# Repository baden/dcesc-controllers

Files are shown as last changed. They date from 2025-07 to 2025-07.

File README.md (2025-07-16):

# dcesc-controllers

Тут буде і плата і програма.

## Так. Шось в процесі ми якось дішли до потужної плати. І назва трохи не відповідає.

## Мотори

Експериментую з моторами з редуктором.

Починаю експерімент з [JGA25-370](https://www.aliexpress.com/item/1005006961499514.html)
та [GA24Y-370](https://www.aliexpress.com/item/1005005835525169.html)

на двигунах діаметром 24.4мм

Ціль:
напруга живлення - 24В
струм - 3А
керування - RS485

Хотілось би CAN, але поки не підібрани варіанти конролера.

Пропонується варіанти драйвера двигуна:

- [DRV8870DDAR](https://www.kosmodrom.ua/mikroshema-kontrolera-dviguna/drv8870ddar-4.html) - 12грн
- [DRV8874PWPR](https://www.kosmodrom.ua/mikroshema-kontrolera-dviguna/drv8874pwpr-2.html) - 44грн

# Робимо цю версію на готових драйверах. Бо два-три мотори на одному мікроконтроллері то дуже складно.

## На майбутньє, може буду підбирати якісь китайські компоненти, бо ціна на амеріканських брендах виходить якась зовсім неадекватна.

## Встановлення інструментів

https://github.com/riscv-software-src/homebrew-riscv

```bash
brew tap riscv-software-src/riscv
brew install riscv-tools
brew install riscv-openocd
brew test riscv-tools
/opt/homebrew/opt/riscv-gnu-toolchain/bin/riscv64-unknown-elf-gcc --version
```

/opt/homebrew/opt/riscv-openocd/bin/openocd

## Обираємо мікроконтролер

Я ще не визначився, чи треба робити виключно на CAN, чи може обійтись RS485.

- Оцей мабуть ідеальний для контролеру двигуна
https://www.kosmodrom.ua/mikrokontroler/stm32g431cbt6.html

Для плат с готовий драйвером двигуна, контролер:

https://www.kosmodrom.ua/mikrokontroler/stm32f042f6p6.html

- Шось мегапопулярне, але не впевнен шо воно.
https://www.kosmodrom.ua/mikrokontroler/stm32f103c8t6.html

- Ексотіка для ізвращьєнців
https://www.kosmodrom.ua/mikrokontroler/gd32f103cbt6-2.html

Ще подивлюсь на цей: CH32V203. Здається є сумісний по ногам як STM, так і GD, так і AT

## Обираємо транзистор на потужну плату

### 60 V

https://www.kosmodrom.ua/tranzistor-poloviy-mosfet/60n06-2.html, 39 nC, 14mOhm
https://www.kosmodrom.ua/tranzistor-poloviy-mosfet/csd18537nq5a-2.html, 18 nC, 13mOhm
https://www.kosmodrom.ua/tranzistor-poloviy-mosfet/aon7262e-2.html, 45 nC, 6.2mOhm

## Драйвер MOSFET

https://www.kosmodrom.ua/drayveri-igbt-mosfet/eg3013s-2.html, 0.8/1.0A,

## Драйвер CAN-шини.

Треба або взяти 3.3В CAN, ти живити окремим живленням 5V, та обирати з Vio, чи согласовувати рівні.

https://www.kosmodrom.ua/interfeys-can-2/sn65hvd230dr.html
https://www.kosmodrom.ua/interfeys-can-2/sn65hvd232d.html (no stb and sleep)

## Готовий контролер на слабкіший мотор

https://www.kosmodrom.ua/mikroshema-kontrolera-dviguna/drv8870ddar-4.html, 3.6А, 45V
https://www.kosmodrom.ua/mikroshema-kontrolera-dviguna/drv8870ddar-2.html,
https://www.kosmodrom.ua/mikroshema-kontrolera-dviguna/drv8874pwpr-2.html, 6А, 37V

## Всіляке різне

https://www.kosmodrom.ua/tranzistor-poloviy-mosfet/ao4828.html, дешевий сдвоєний мосфет на драйвер до 3А.

https://www.kosmodrom.ua/stabilizator-naprugi/ht7533s-umw-2.html, Стабілізатор напруги на процесор, 3.3V, 0.1A

## Во, подивиться це

https://github.com/wagiminator/CH32V003-GameConsole/tree/main

Ще це:
https://github.com/wagiminator/MCU-Templates

Ще тут купа посилань:
https://github.com/wagiminator/Development-Boards/tree/main/CH32V003A4M6_DevBoard

https://github.com/AlessandroAU/ESP32-CRSF-Packet-Gen/blob/master/CRSF_testcode/CRSF.h
https://px4.github.io/Firmware-Doxygen/d9/dd2/crsf_8cpp_source.html

https://github.com/vedderb/bldc_uart_comm_stm32f4_discovery/blob/c19a6283e187040f25aa52e213673938db054d06/bldc_interface.c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

https://vedder.se/2015/10/communicating-with-the-vesc-using-uart/

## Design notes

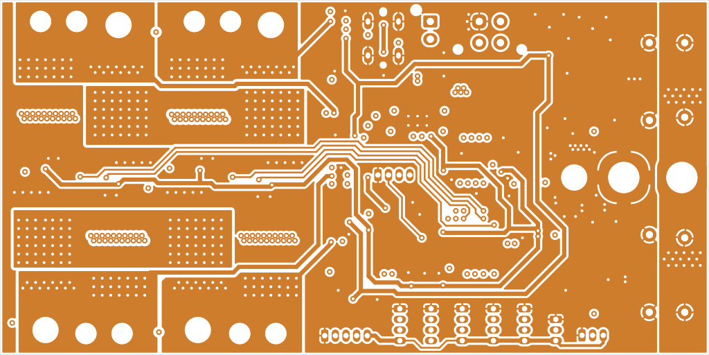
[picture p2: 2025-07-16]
dist/dcesc-ga25/check/dcesc-ga25-In2.Cu.png

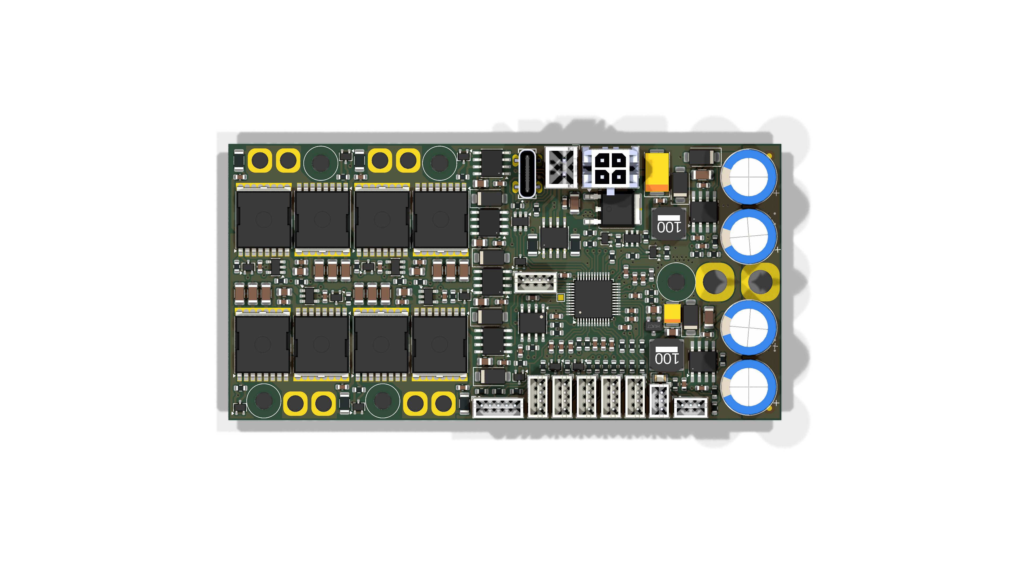
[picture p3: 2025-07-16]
boards/dcesc-ga25/dcesc-ga25-v0/dcesc-ga25-0.png

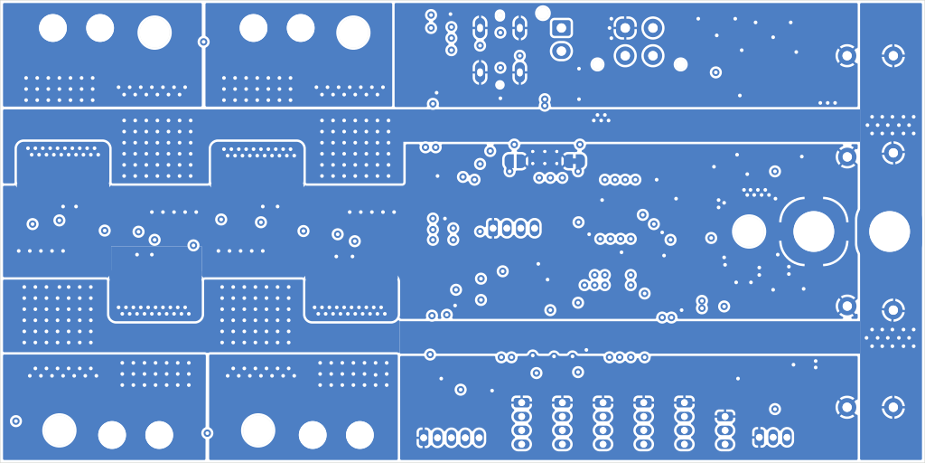
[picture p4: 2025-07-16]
dist/dcesc-ga25/check/dcesc-ga25-B.Cu.png

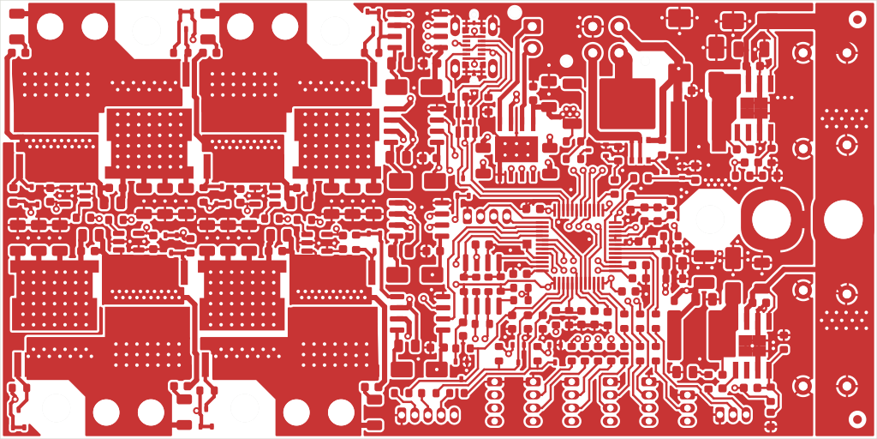
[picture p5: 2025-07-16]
dist/dcesc-ga25/check/dcesc-ga25-F.Cu.png

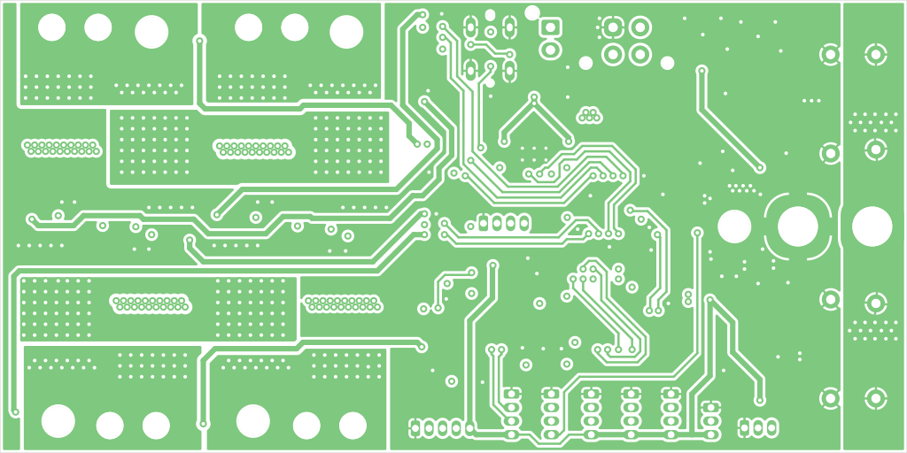
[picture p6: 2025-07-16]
dist/dcesc-ga25/check/dcesc-ga25-In1.Cu.png

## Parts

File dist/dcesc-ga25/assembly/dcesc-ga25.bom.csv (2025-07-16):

Refs | Value | Footprint | Qty | DNP
C1 | 10uF | Capacitor_SMD:C_1206_3216Metric | 1
C2 | 10uF | Capacitor_SMD:C_1206_3216Metric | 1
C3 | 0.1uF | Capacitor_SMD:C_0603_1608Metric | 1
C4 | 0.1uF | Capacitor_SMD:C_0603_1608Metric | 1
C5 | 0.1uF | Capacitor_SMD:C_0603_1608Metric | 1
C6 | 0.1uF | Capacitor_SMD:C_0603_1608Metric | 1
C7 | 82p | Capacitor_SMD:C_0603_1608Metric | 1
C8 | 82p | Capacitor_SMD:C_0603_1608Metric | 1
C9 | 100uF | Capacitor_Tantalum_SMD:CP_EIA-7343-15_Kemet-W | 1
C10 | 0.1uF | Capacitor_SMD:C_0603_1608Metric | 1
C11 | 100uF | Capacitor_Tantalum_SMD:CP_EIA-3528-12_Kemet-T | 1
C12 | 10uF | Capacitor_SMD:C_0805_2012Metric | 1
C13 | 10uF | Capacitor_SMD:C_0805_2012Metric | 1
C14 | 10uF | Capacitor_SMD:C_1206_3216Metric | 1
C15 | 0.1uF | Capacitor_SMD:C_0603_1608Metric | 1
C16 | 0.1uF | Capacitor_SMD:C_0603_1608Metric | 1
C17 | 0.1uF | Capacitor_SMD:C_0603_1608Metric | 1
C18 | 0.1uF | Capacitor_SMD:C_0603_1608Metric | 1
C19 | 0.1uF | Capacitor_SMD:C_0603_1608Metric | 1
C20 | 0.1uF | Capacitor_SMD:C_0603_1608Metric | 1
C21 | 0.1uF | Capacitor_SMD:C_0603_1608Metric | 1
C22 | 10nF | Capacitor_SMD:C_0603_1608Metric | 1
C23 | 10nF | Capacitor_SMD:C_0603_1608Metric | 1
C24 | 10nF | Capacitor_SMD:C_0603_1608Metric | 1
C25 | 0.1uF | Capacitor_SMD:C_0603_1608Metric | 1
C26 | 10nF | Capacitor_SMD:C_0603_1608Metric | 1
C27 | 0.1uF | Capacitor_SMD:C_0603_1608Metric | 1
C28 | 0.1uF | Capacitor_SMD:C_0603_1608Metric | 1
C29 | 0.1uF | Capacitor_SMD:C_0603_1608Metric | 1
C30 | 0.1uF | Capacitor_SMD:C_0603_1608Metric | 1
C31 | 0.1uF | Capacitor_SMD:C_0603_1608Metric | 1
C32 | 0.1uF | Capacitor_SMD:C_0603_1608Metric | 1
C33 | 0.1uF | Capacitor_SMD:C_0603_1608Metric | 1
C34 | 0.1uF | Capacitor_SMD:C_0603_1608Metric | 1
C35 | 0.1uF | Capacitor_SMD:C_0603_1608Metric | 1
C36 | 0.1uF | Capacitor_SMD:C_0603_1608Metric | 1
C37 | 0.1uF | Capacitor_SMD:C_0603_1608Metric | 1
C38 | 0.1uF | Capacitor_SMD:C_0603_1608Metric | 1
C39 | 0.1uF | Capacitor_SMD:C_0603_1608Metric | 1
C40 | 0.1uF | Capacitor_SMD:C_0603_1608Metric | 1
C41 | 33nF | Capacitor_SMD:C_0603_1608Metric | 1
C42 | 33nF | Capacitor_SMD:C_0603_1608Metric | 1
C43 | 33nF | Capacitor_SMD:C_0603_1608Metric | 1
C44 | 33nF | Capacitor_SMD:C_0603_1608Metric | 1
C45 | 10uF | Capacitor_SMD:C_0805_2012Metric | 1
C46 | 10uF | Capacitor_SMD:C_0805_2012Metric | 1
C47 | 10uF | Capacitor_SMD:C_0805_2012Metric | 1
C48 | 10uF | Capacitor_SMD:C_0805_2012Metric | 1
C49 | 1uF | Capacitor_SMD:C_0805_2012Metric | 1
C50 | 1uF | Capacitor_SMD:C_0805_2012Metric | 1
C51 | 1uF | Capacitor_SMD:C_0805_2012Metric | 1
C52 | 1uF | Capacitor_SMD:C_0805_2012Metric | 1
C53 | 10uF | Capacitor_SMD:C_1206_3216Metric | 1
C54 | 10uF | Capacitor_SMD:C_1206_3216Metric | 1
C55 | 10uF | Capacitor_SMD:C_1206_3216Metric | 1
C56 | 10uF | Capacitor_SMD:C_1206_3216Metric | 1
C57 | 10uF | Capacitor_SMD:C_1206_3216Metric | 1
C58 | 10uF | Capacitor_SMD:C_1206_3216Metric | 1
C59 | 10uF | Capacitor_SMD:C_1206_3216Metric | 1
C60 | 10uF | Capacitor_SMD:C_1206_3216Metric | 1
C61 | 10uF | Capacitor_SMD:C_1206_3216Metric | 1
C62 | 10uF | Capacitor_SMD:C_1206_3216Metric | 1
C63 | 10uF | Capacitor_SMD:C_1206_3216Metric | 1
C64 | 10uF | Capacitor_SMD:C_1206_3216Metric | 1
C65 | 220uF | Capacitor_THT:CP_Radial_D10.0mm_P5.00mm | 1
C66 | 220uF | Capacitor_THT:CP_Radial_D10.0mm_P5.00mm | 1
C67 | 220uF | Capacitor_THT:CP_Radial_D10.0mm_P5.00mm | 1
C68 | 220uF | Capacitor_THT:CP_Radial_D10.0mm_P5.00mm | 1
C69 | 3.3nF | Capacitor_SMD:C_0603_1608Metric | 1
C70 | 3.3nF | Capacitor_SMD:C_0603_1608Metric | 1
C71 | 3.3nF | Capacitor_SMD:C_0603_1608Metric | 1
C72 | 3.3nF | Capacitor_SMD:C_0603_1608Metric | 1
D1 | SMAJ28A | Diode_SMD:D_SMA | 1
D2 | SS24 | Diode_SMD:D_SMA | 1
D3 | SS24 | Diode_SMD:D_SMA | 1
D4 | BAT54SW | Package_TO_SOT_SMD:SOT-323_SC-70 | 1
D5 | BAT54SW | Package_TO_SOT_SMD:SOT-323_SC-70 | 1
D6 | BAT54SW | Package_TO_SOT_SMD:SOT-323_SC-70 | 1
D7 | BAT54AW | Package_TO_SOT_SMD:SOT-323_SC-70 | 1
D8 | BAT54AW | Package_TO_SOT_SMD:SOT-323_SC-70 | 1
D9 | BAT54AW | Package_TO_SOT_SMD:SOT-323_SC-70 | 1
D10 | BAT54AW | Package_TO_SOT_SMD:SOT-323_SC-70 | 1
D11 | BAT54AW | Package_TO_SOT_SMD:SOT-323_SC-70 | 1
D12 | BAT54AW | Package_TO_SOT_SMD:SOT-323_SC-70 | 1
D13 | BAT54AW | Package_TO_SOT_SMD:SOT-323_SC-70 | 1
D14 | BAT54AW | Package_TO_SOT_SMD:SOT-323_SC-70 | 1
D15 | SS24 | Diode_SMD:D_SMA | 1
D16 | SS24 | Diode_SMD:D_SMA | 1
D17 | SS24 | Diode_SMD:D_SMA | 1
D18 | SS24 | Diode_SMD:D_SMA | 1
D19 | BAT54AW | Package_TO_SOT_SMD:SOT-323_SC-70 | 1
D20 | LED | LED_SMD:LED_0805_2012Metric | 1
FB1 | FerriteBead | Inductor_SMD:L_0603_1608Metric | 1
J1 | Jumper_2_Open | Jumper:SolderJumper-2_P1.3mm_Open_RoundedPad1.0x1.5mm | 1
J2 | Jumper_2_Bridged | Jumper:SolderJumper-2_P1.3mm_Bridged_RoundedPad1.0x1.5mm | 1
J3 | Conn_01x01_Socket | Connector_Wire:SolderWire-2.5sqmm_1x01_D2.4mm_OD4.4mm | 1
J4 | Conn_01x01_Socket | Connector_Wire:SolderWire-2.5sqmm_1x01_D2.4mm_OD4.4mm | 1
J5 | Conn_01x01_Socket | Connector_Wire:SolderWire-2.5sqmm_1x01_D2.4mm_OD4.4mm | 1
J6 | Conn_01x01_Socket | Connector_Wire:SolderWire-2.5sqmm_1x01_D2.4mm_OD4.4mm | 1
J7 | Conn_01x01_Socket | Connector_Wire:SolderWire-2.5sqmm_1x01_D2.4mm_OD4.4mm | 1
J8 | Conn_01x01_Socket | Connector_Wire:SolderWire-2.5sqmm_1x01_D2.4mm_OD4.4mm | 1
J9 | Conn_01x01_Socket | Connector_Wire:SolderWire-2.5sqmm_1x01_D2.4mm_OD4.4mm | 1
J10 | Conn_01x01_Socket | Connector_Wire:SolderWire-2.5sqmm_1x01_D2.4mm_OD4.4mm | 1
J18 | Conn_01x01_Socket | Connector_Wire:SolderWire-6sqmm_1x01_D3.5mm_OD7mm | 1
J19 | Conn_01x01_Socket | Connector_Wire:SolderWire-6sqmm_1x01_D3.5mm_OD7mm | 1
L1 | 10uH | locals:Inductor_NR6028T100M | 1
L2 | 10uH | locals:Inductor_NR6028T100M | 1
R1 | 30k | Resistor_SMD:R_0603_1608Metric | 1
R2 | 3.3k | Resistor_SMD:R_0603_1608Metric | 1
R3 | 100k | Resistor_SMD:R_0603_1608Metric | 1
R4 | 10k | Resistor_SMD:R_0603_1608Metric | 1
R5 | 3.3k | Resistor_SMD:R_0603_1608Metric | 1
R6 | 100k | Resistor_SMD:R_0603_1608Metric | 1
R7 | 30k | Resistor_SMD:R_0603_1608Metric | 1
R8 | 30k | Resistor_SMD:R_0603_1608Metric | 1
R9 | 100k | Resistor_SMD:R_0603_1608Metric | 1
R10 | 100k | Resistor_SMD:R_0603_1608Metric | 1
R11 | 100k | Resistor_SMD:R_0603_1608Metric | 1
R12 | 30k | Resistor_SMD:R_0603_1608Metric | 1
R13 | 30k | Resistor_SMD:R_0603_1608Metric | 1
R14 | 0.51R | Resistor_SMD:R_1206_3216Metric | 1
R15 | 1R | Resistor_SMD:R_1206_3216Metric | 1
R16 | 120 | Resistor_SMD:R_0603_1608Metric | 1
R17 | 330k | Resistor_SMD:R_0603_1608Metric | 1
R18 | 10k | Resistor_SMD:R_0603_1608Metric | 1
R19 | 10k | Resistor_SMD:R_0603_1608Metric | 1
R20 | 10k | Resistor_SMD:R_0603_1608Metric | 1
R21 | 30k | Resistor_SMD:R_0603_1608Metric | 1
R22 | 100k | Resistor_SMD:R_0603_1608Metric | 1
R23 | 100k | Resistor_SMD:R_0603_1608Metric | 1
R24 | 100k | Resistor_SMD:R_0603_1608Metric | 1
R25 | 100 | Resistor_SMD:R_0603_1608Metric | 1
R26 | 100 | Resistor_SMD:R_0603_1608Metric | 1
R27 | 100 | Resistor_SMD:R_0603_1608Metric | 1
R28 | 100 | Resistor_SMD:R_0603_1608Metric | 1
R29 | 100 | Resistor_SMD:R_0603_1608Metric | 1
R30 | 100 | Resistor_SMD:R_0603_1608Metric | 1
R31 | 100 | Resistor_SMD:R_0603_1608Metric | 1
R32 | 100 | Resistor_SMD:R_0603_1608Metric | 1
R33 | 100 | Resistor_SMD:R_0603_1608Metric | 1
R34 | 100 | Resistor_SMD:R_0603_1608Metric | 1
R35 | 330k | Resistor_SMD:R_0603_1608Metric | 1
R36 | 30k | Resistor_SMD:R_0603_1608Metric | 1
R37 | 1k | Resistor_SMD:R_0603_1608Metric | 1
R38 | 1k | Resistor_SMD:R_0603_1608Metric | 1
R39 | 1k | Resistor_SMD:R_0603_1608Metric | 1
R40 | 1k | Resistor_SMD:R_0603_1608Metric | 1
R41 | 1k | Resistor_SMD:R_0603_1608Metric | 1
R42 | 100k | Resistor_SMD:R_0603_1608Metric | 1
R43 | 10 | Resistor_SMD:R_0603_1608Metric | 1
R44 | 10 | Resistor_SMD:R_0603_1608Metric | 1
R45 | 10 | Resistor_SMD:R_0603_1608Metric | 1
R46 | 10 | Resistor_SMD:R_0603_1608Metric | 1
R47 | 10 | Resistor_SMD:R_0603_1608Metric | 1
R48 | 10 | Resistor_SMD:R_0603_1608Metric | 1
R49 | 10 | Resistor_SMD:R_0603_1608Metric | 1
R50 | 10 | Resistor_SMD:R_0603_1608Metric | 1
R51 | 3 | Resistor_SMD:R_1206_3216Metric | 1
R52 | 3 | Resistor_SMD:R_1206_3216Metric | 1
R53 | 3 | Resistor_SMD:R_1206_3216Metric | 1
R54 | 3 | Resistor_SMD:R_1206_3216Metric | 1
R55 | 5.1k | Resistor_SMD:R_0603_1608Metric | 1
R56 | 5.1k | Resistor_SMD:R_0603_1608Metric | 1
R57 | 3.3k | Resistor_SMD:R_0603_1608Metric | 1
T1 | IPT012N08N5 | Package_TO_SOT_SMD:Infineon_PG-HSOF-8-1 | 1
T2 | IPT012N08N5 | Package_TO_SOT_SMD:Infineon_PG-HSOF-8-1 | 1
T3 | IPT012N08N5 | Package_TO_SOT_SMD:Infineon_PG-HSOF-8-1 | 1
T4 | IPT012N08N5 | Package_TO_SOT_SMD:Infineon_PG-HSOF-8-1 | 1
T5 | IPT012N08N5 | Package_TO_SOT_SMD:Infineon_PG-HSOF-8-1 | 1
T6 | IPT012N08N5 | Package_TO_SOT_SMD:Infineon_PG-HSOF-8-1 | 1
T7 | IPT012N08N5 | Package_TO_SOT_SMD:Infineon_PG-HSOF-8-1 | 1
T8 | IPT012N08N5 | Package_TO_SOT_SMD:Infineon_PG-HSOF-8-1 | 1
T9 | BC847AW | Package_TO_SOT_SMD:SOT-323_SC-70 | 1
T10 | BC847AW | Package_TO_SOT_SMD:SOT-323_SC-70 | 1
T11 | IRF5803TRPBF | Package_SO:TSOP-6_1.65x3.05mm_P0.95mm | 1
T12 | AOD4185 | Package_TO_SOT_SMD:TO-252-2 | 1
TP1 | BOOT0 | TestPoint:TestPoint_Pad_1.0x1.0mm | 1
U1 | ST1S14PHR | Package_SO:TI_SO-PowerPAD-8 | 1
U2 | ST1S14PHR | Package_SO:TI_SO-PowerPAD-8 | 1
U3 | MCP1703A-3302 | locals:MCP1703 | 1
U4 | STM32G431C8Tx | Package_QFP:LQFP-48_7x7mm_P0.5mm | 1
U5 | INA180A4 | Package_TO_SOT_SMD:SOT-23-5 | 1
U6 | INA180A4 | Package_TO_SOT_SMD:SOT-23-5 | 1
U7 | INA180A4 | Package_TO_SOT_SMD:SOT-23-5 | 1
U8 | INA180A4 | Package_TO_SOT_SMD:SOT-23-5 | 1
U9 | EG3112 | Package_SO:SOP-8_3.9x4.9mm_P1.27mm | 1
U10 | EG3112 | Package_SO:SOP-8_3.9x4.9mm_P1.27mm | 1
U11 | EG3112 | Package_SO:SOP-8_3.9x4.9mm_P1.27mm | 1
U12 | EG3112 | Package_SO:SOP-8_3.9x4.9mm_P1.27mm | 1
U13 | DRV8870DDA | Package_SO:Texas_HTSOP-8-1EP_3.9x4.9mm_P1.27mm_EP2.95x4.9mm_Mask2.4x3.1mm_ThermalVias | 1
U14 | ATA6561-GAQW-N | Package_SO:SOIC-8_3.9x4.9mm_P1.27mm | 1
U15 | USBLC6-2SC6 | Package_TO_SOT_SMD:SOT-23-6 | 1
X1 | Conn_02x02_Top_Bottom | Connector_Molex:Molex_Micro-Fit_3.0_43045-0412_2x02_P3.00mm_Vertical | 1
X2 | Conn_01x03 | Connector_JST:JST_XH_B2B-XH-AM_1x02_P2.50mm_Vertical | 1
X3 | Conn_01x03 | Connector_JST:JST_ZH_B4B-ZR_1x04_P1.50mm_Vertical | 1
X4 | Conn_01x03 | Connector_JST:JST_ZH_B4B-ZR_1x04_P1.50mm_Vertical | 1
X5 | Conn_01x03 | Connector_JST:JST_ZH_B4B-ZR_1x04_P1.50mm_Vertical | 1
X6 | Conn_01x03 | Connector_JST:JST_ZH_B4B-ZR_1x04_P1.50mm_Vertical | 1
X7 | Conn_01x03 | Connector_JST:JST_ZH_B4B-ZR_1x04_P1.50mm_Vertical | 1
X8 | Conn_01x03 | Connector_JST:JST_ZH_B3B-ZR_1x03_P1.50mm_Vertical | 1
X9 | Conn_01x03 | Connector_JST:JST_ZH_B3B-ZR_1x03_P1.50mm_Vertical | 1
X10 | Conn_01x03 | Connector_JST:JST_ZH_B5B-ZR_1x05_P1.50mm_Vertical | 1
X11 | Conn_01x03 | Connector_JST:JST_ZH_B4B-ZR_1x04_P1.50mm_Vertical | 1
X12 | USB4120-03-C_REVA | locals:GCT_USB4120-03-C_REVA | 1

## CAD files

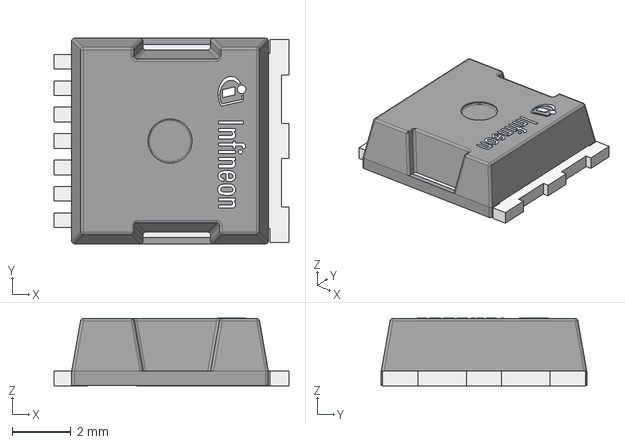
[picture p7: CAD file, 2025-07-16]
boards/dcesc-ga25/3dshapes/PG-HSOF-7-1_Z8B00189574_V04_3D.stp
8.00 x 7.00 x 2.31 mm

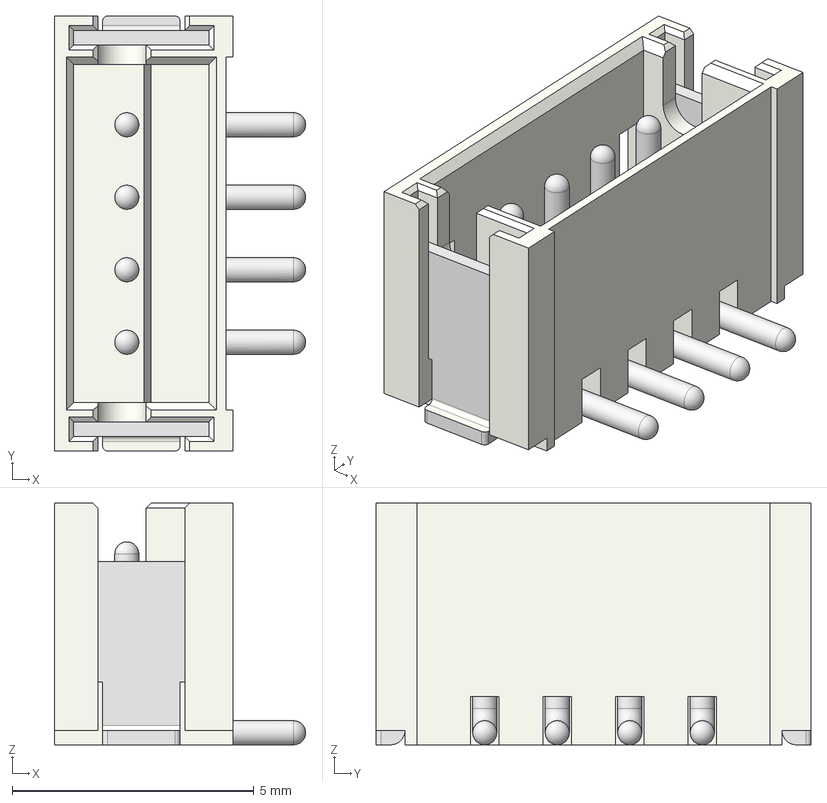
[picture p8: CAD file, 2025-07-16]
boards/dcesc-ga25/3dshapes/B4B-ZR-SM4-TF.step
5.20 x 9.00 x 5.00 mm

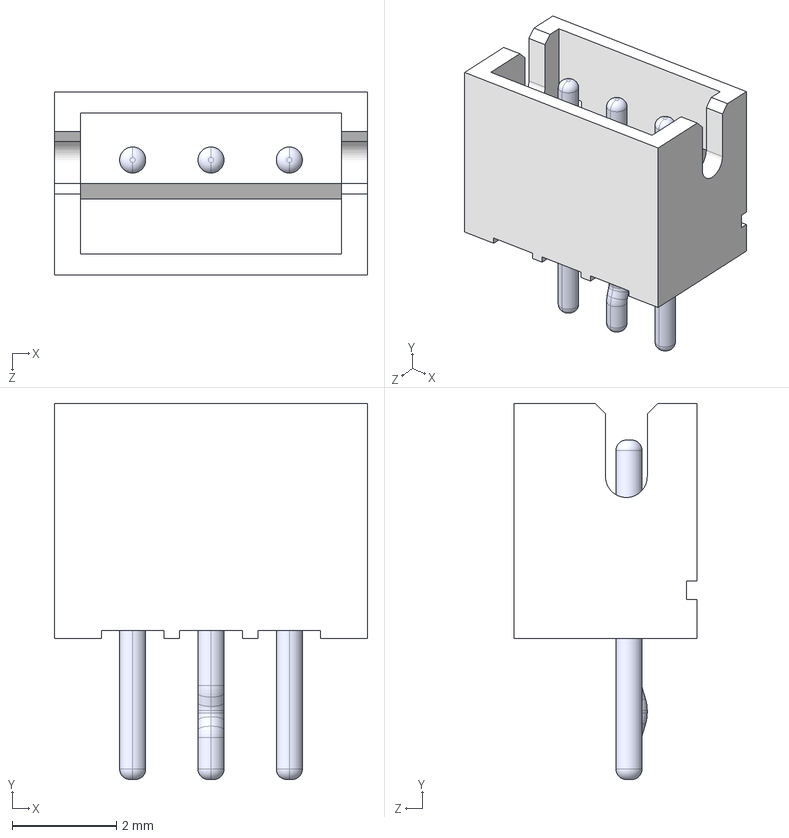
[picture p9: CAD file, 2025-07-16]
boards/dcesc-ga25/3dshapes/B3B-ZR--3DModel-STEP-56544.STEP
6.00 x 7.20 x 3.50 mm
BxB-ZR_3
pin_straight x 2
pin_Bent

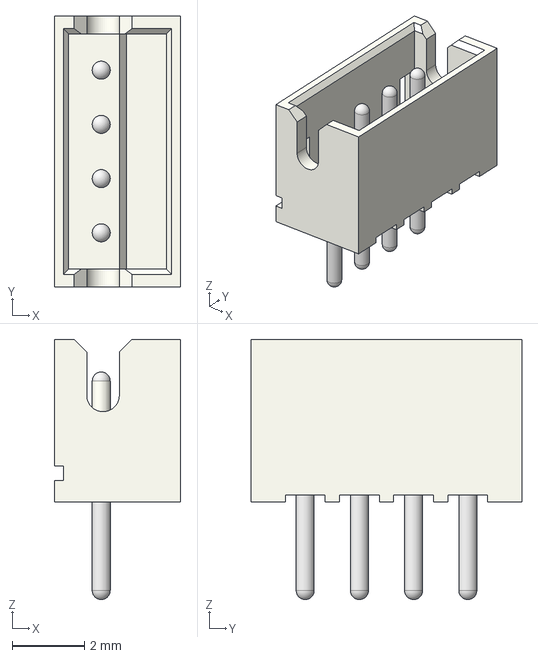
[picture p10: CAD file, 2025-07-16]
boards/dcesc-ga25/3dshapes/B4B-ZR.step
3.50 x 7.50 x 7.20 mm

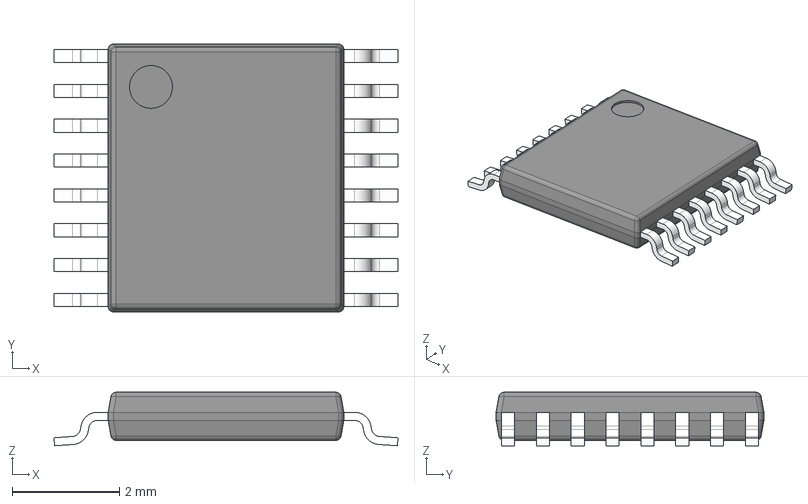
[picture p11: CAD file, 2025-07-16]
boards/dcesc-ga25/3dshapes/PWP0016A.stp
6.42 x 5.00 x 1.00 mm
BODY-SO
LEAD-SO x 16
THERMALPAD-SO
PIN1-ID

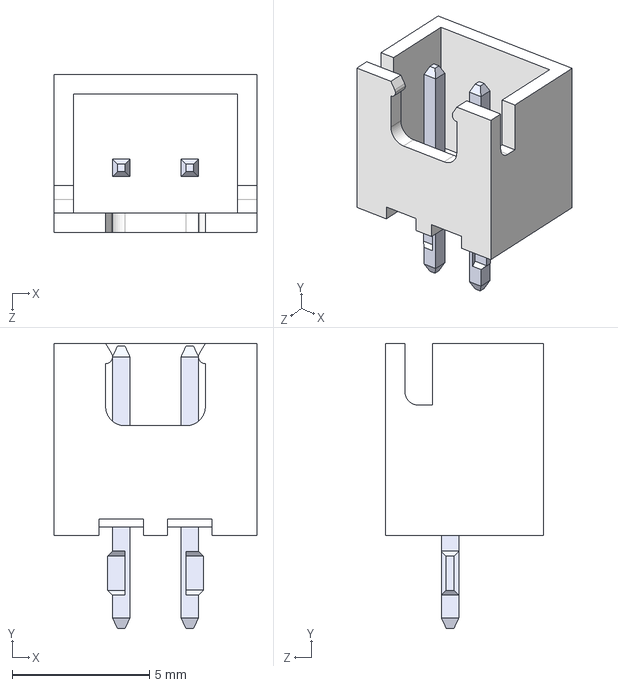
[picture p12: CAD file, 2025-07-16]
boards/dcesc-ga25/3dshapes/B2B-XH-A-LF--SN---3DModel-STEP-269445.STEP
7.40 x 10.4 x 5.75 mm

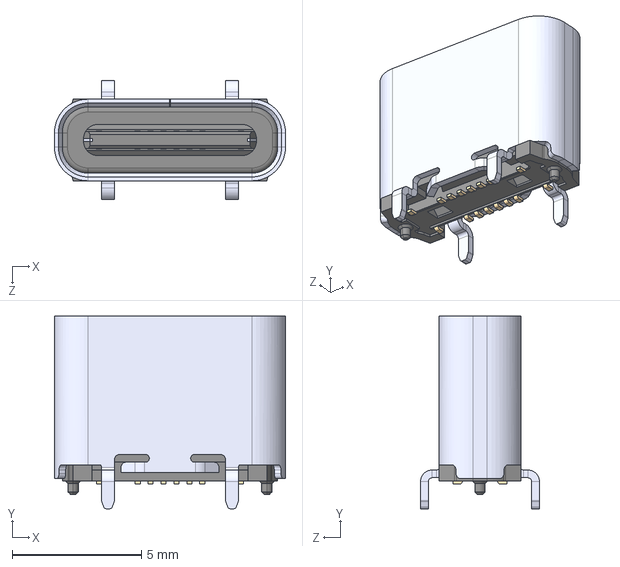
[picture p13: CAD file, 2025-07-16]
boards/dcesc-ga25/3dshapes/USB4120-03-C_REVA.step
8.94 x 7.45 x 4.60 mm

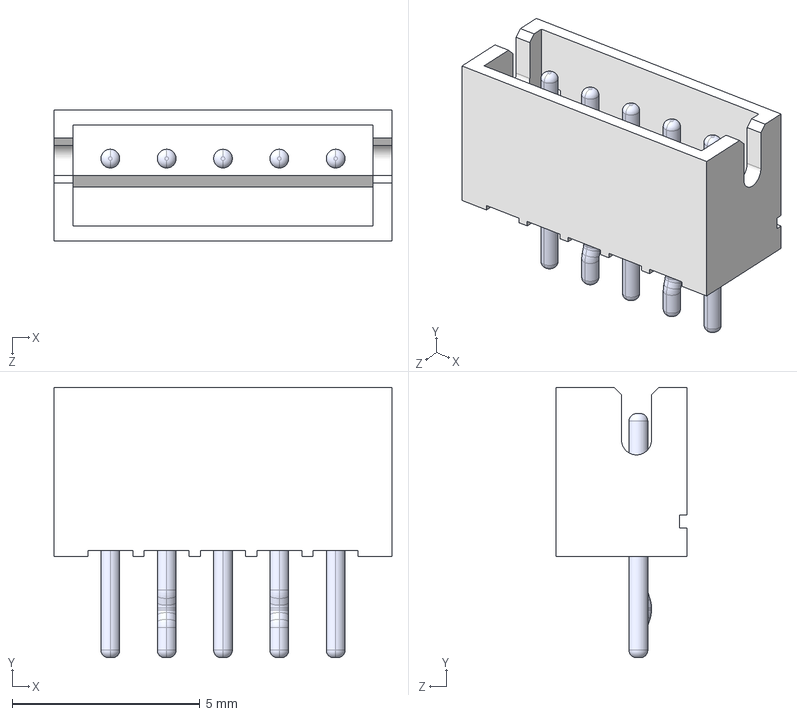
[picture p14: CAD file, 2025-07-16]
boards/dcesc-ga25/3dshapes/B5B-ZR--3DModel-STEP-56544.STEP
9.00 x 7.20 x 3.50 mm
BxB-ZR_5
pin_straight x 3
pin_Bent x 2

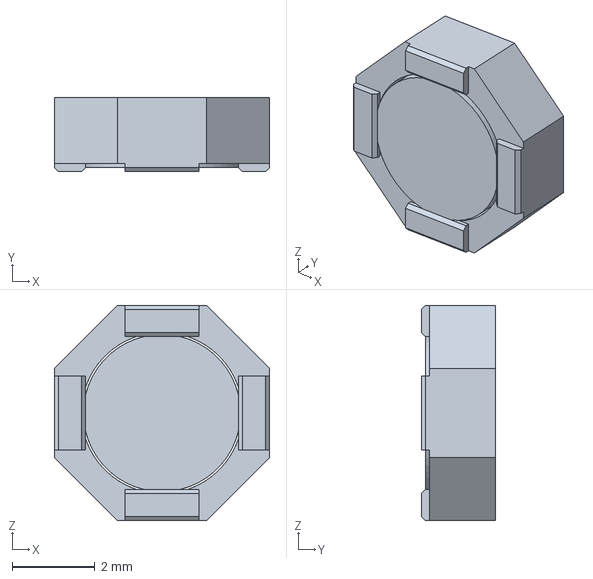
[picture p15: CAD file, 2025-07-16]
boards/dcesc-ga25/3dshapes/sru5018-100y.stp
5.20 x 1.80 x 5.20 mm

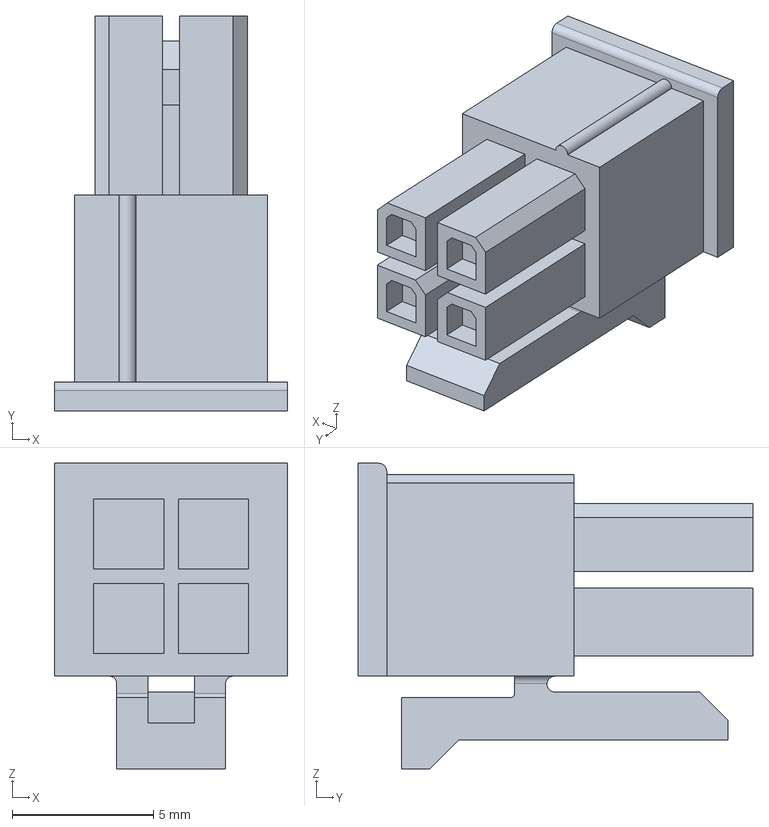
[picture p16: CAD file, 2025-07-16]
boards/dcesc-ga25/3dshapes/43025-0400--3DModel-STEP-390490.STEP
8.27 x 14.0 x 10.8 mm

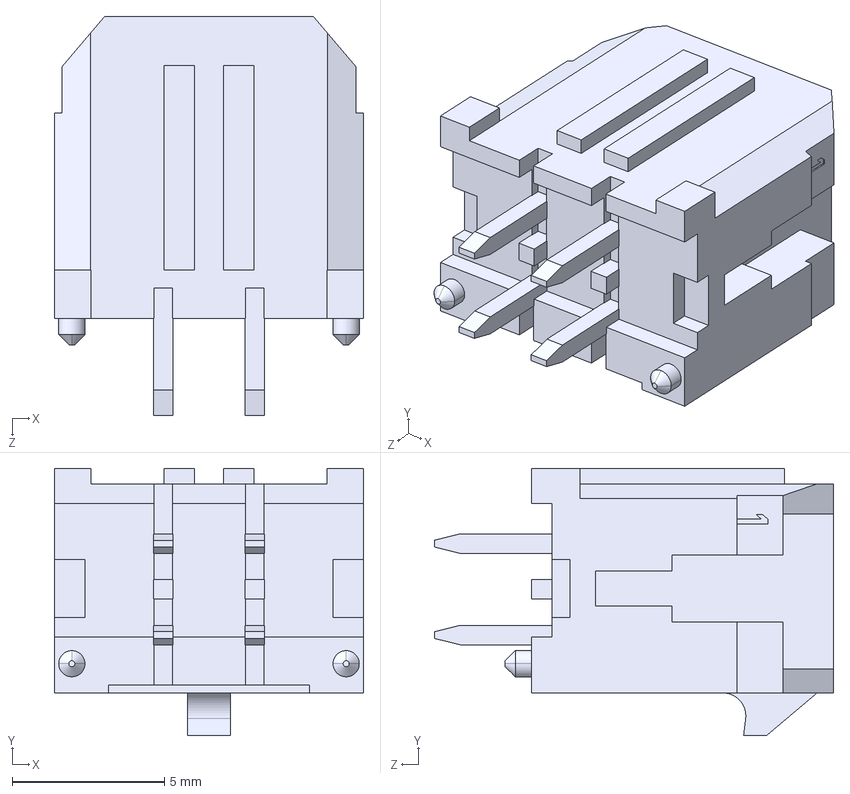
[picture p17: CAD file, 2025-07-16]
boards/dcesc-ga25/3dshapes/430450427--3DModel-STEP-56544.STEP
10.1 x 8.77 x 13.1 mm

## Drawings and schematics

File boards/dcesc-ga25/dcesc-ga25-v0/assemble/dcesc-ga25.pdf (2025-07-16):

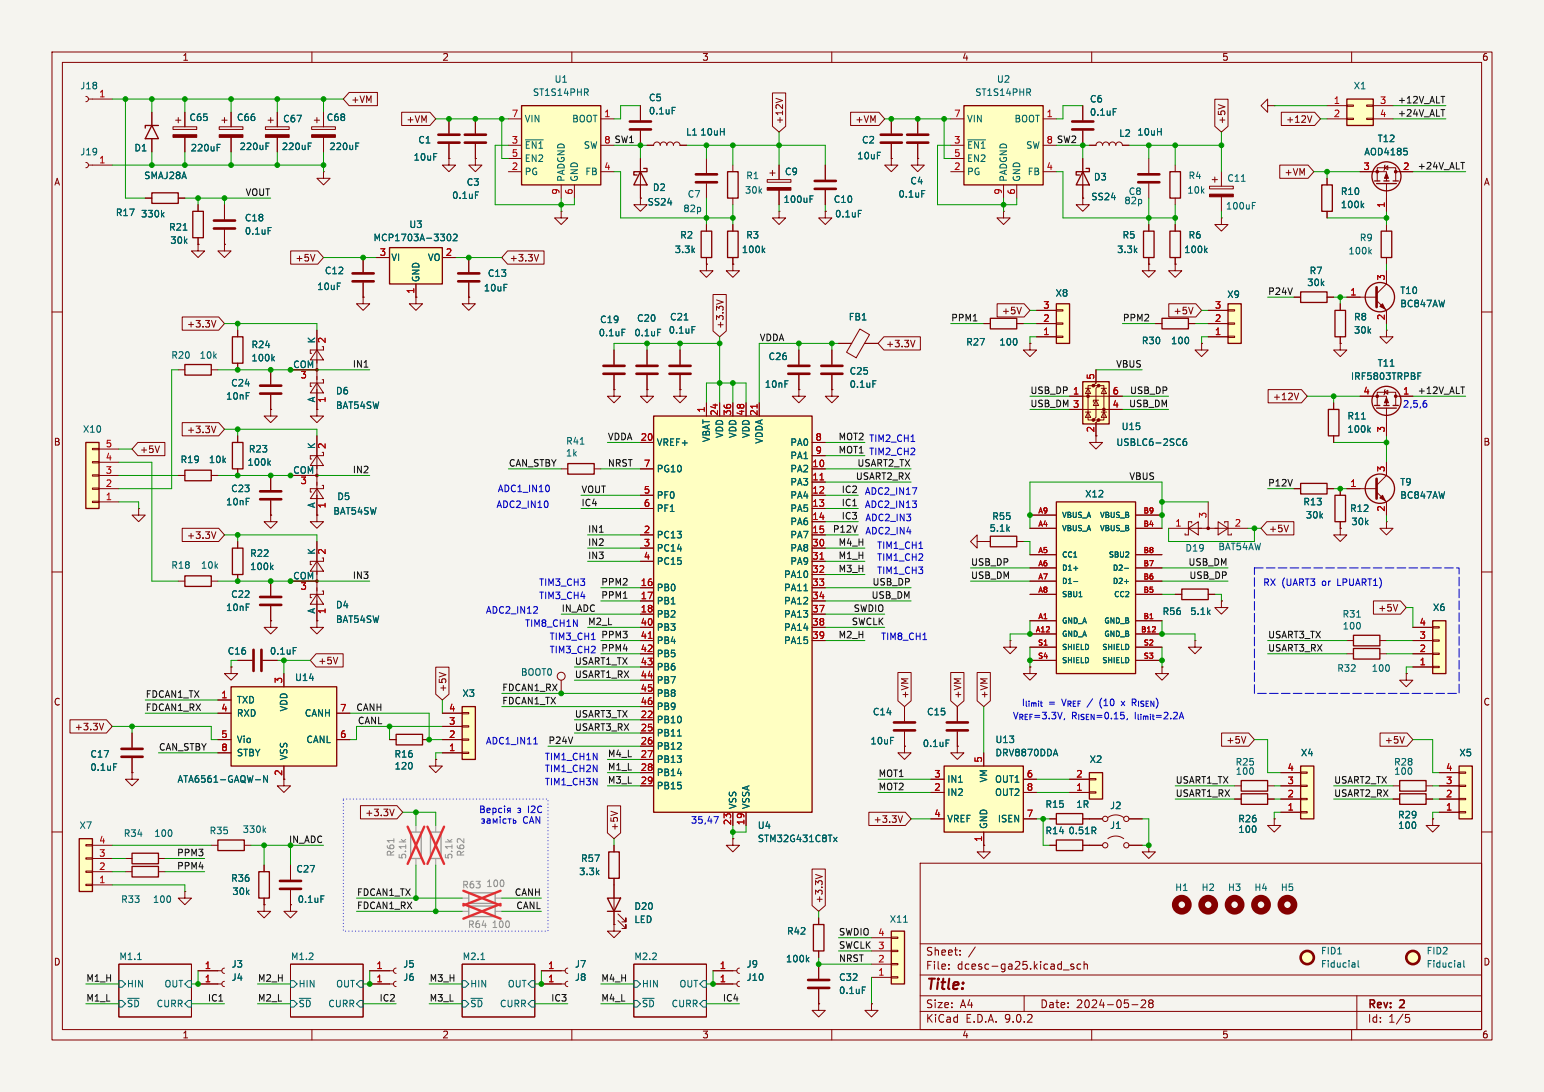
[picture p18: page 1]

1 VDD 24 VDD 36 VSS 23 VDD 48 VSSA 19 VDDA 21 PA0 8 PA1 9 PA2 10 PA3 11 PA4 12 PA5 13 PA6 14 PA7 15 PA8 30 PA9 31 PA10 32 PA11 33 PA12 34 PA13 37 PA14 38 PA15 39 U4STM32G431C8Tx

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

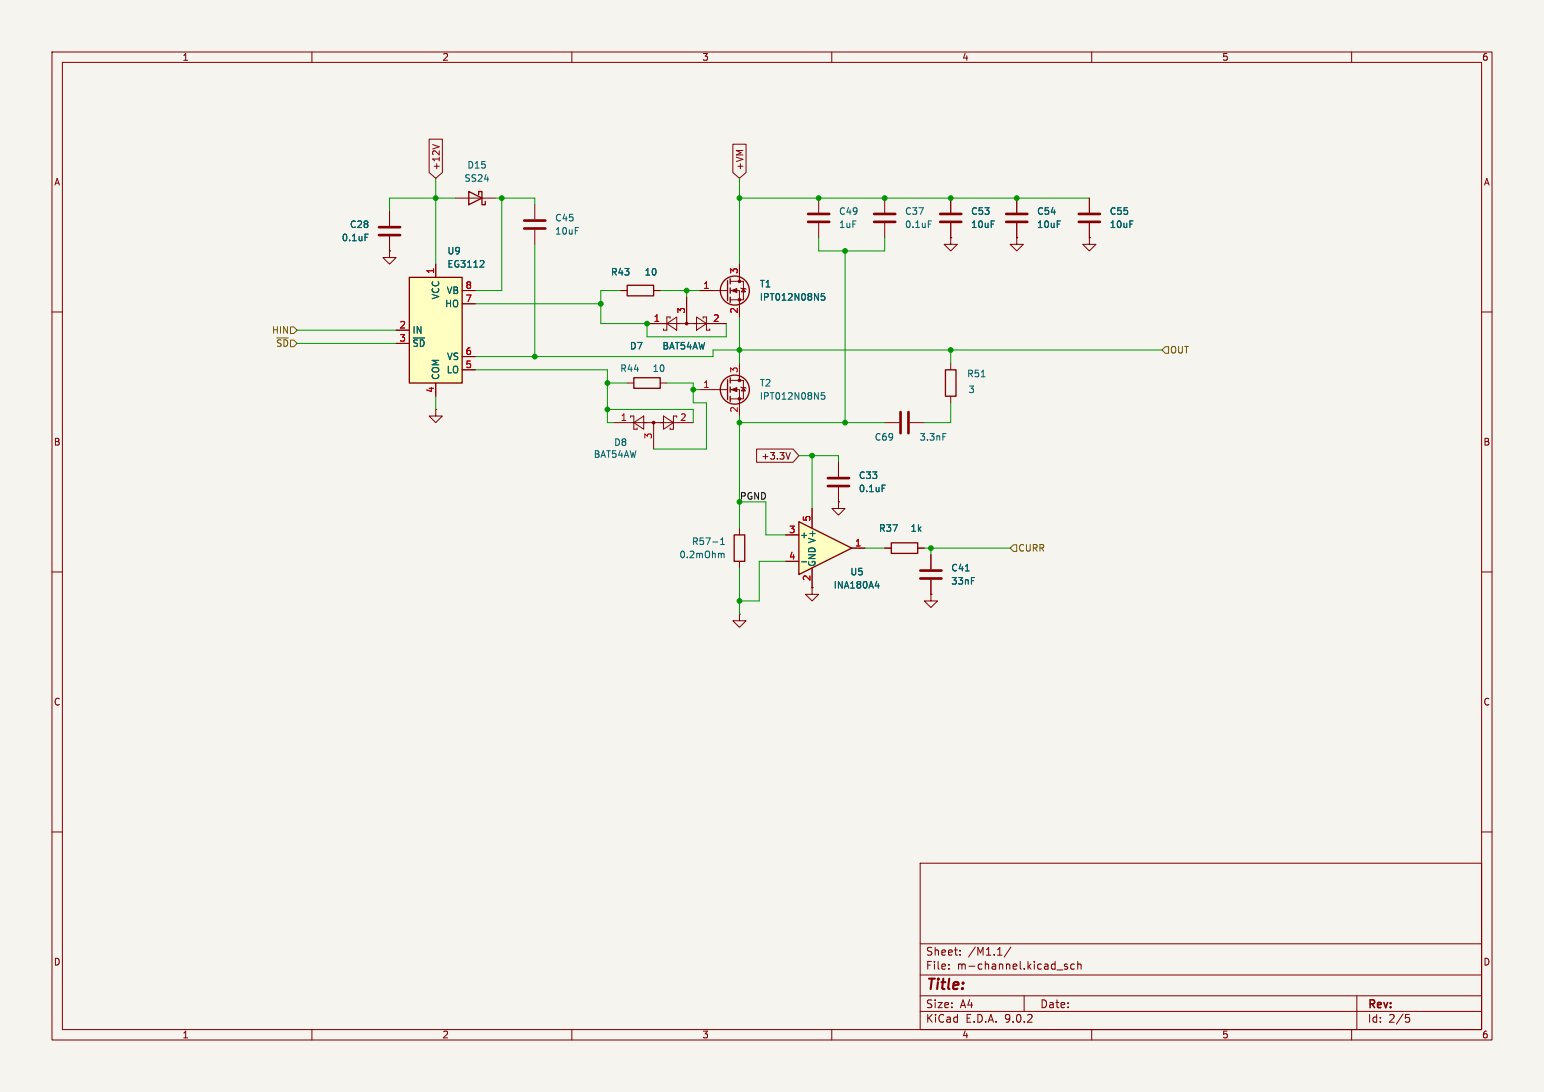
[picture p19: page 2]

Id: 2/5 Title: File: m-channel.kicad_sch Sheet: /M1.1/

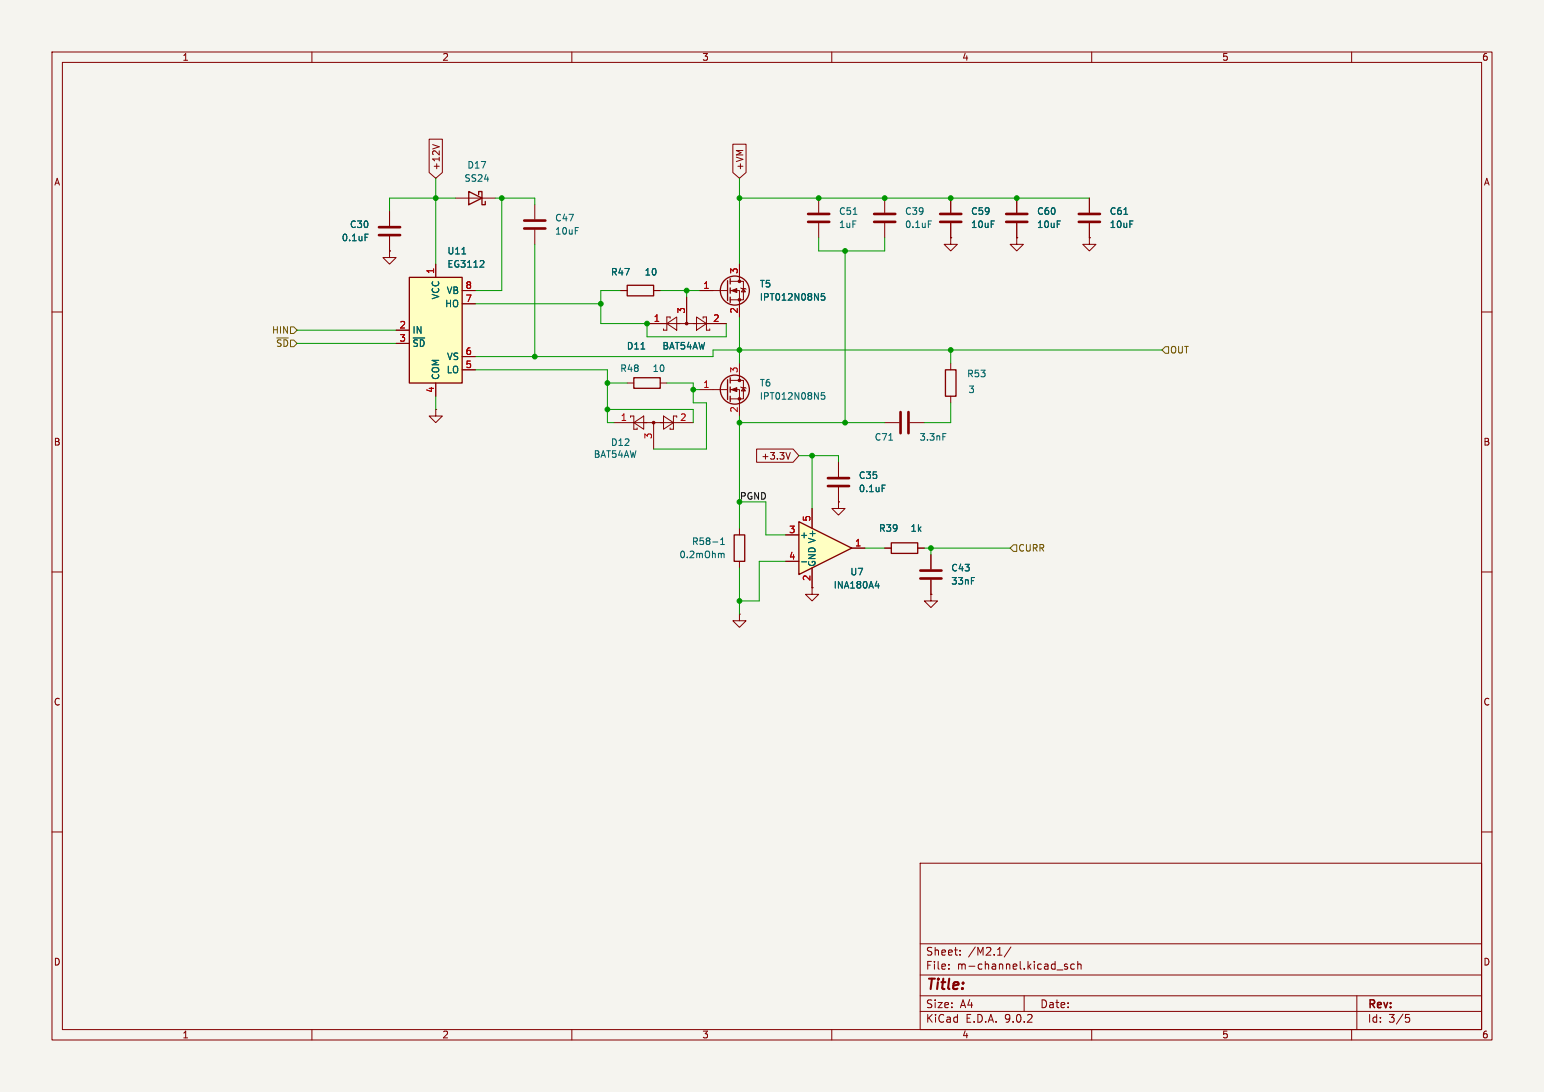
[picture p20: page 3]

Id: 3/5 Title: File: m-channel.kicad_sch Sheet: /M2.1/

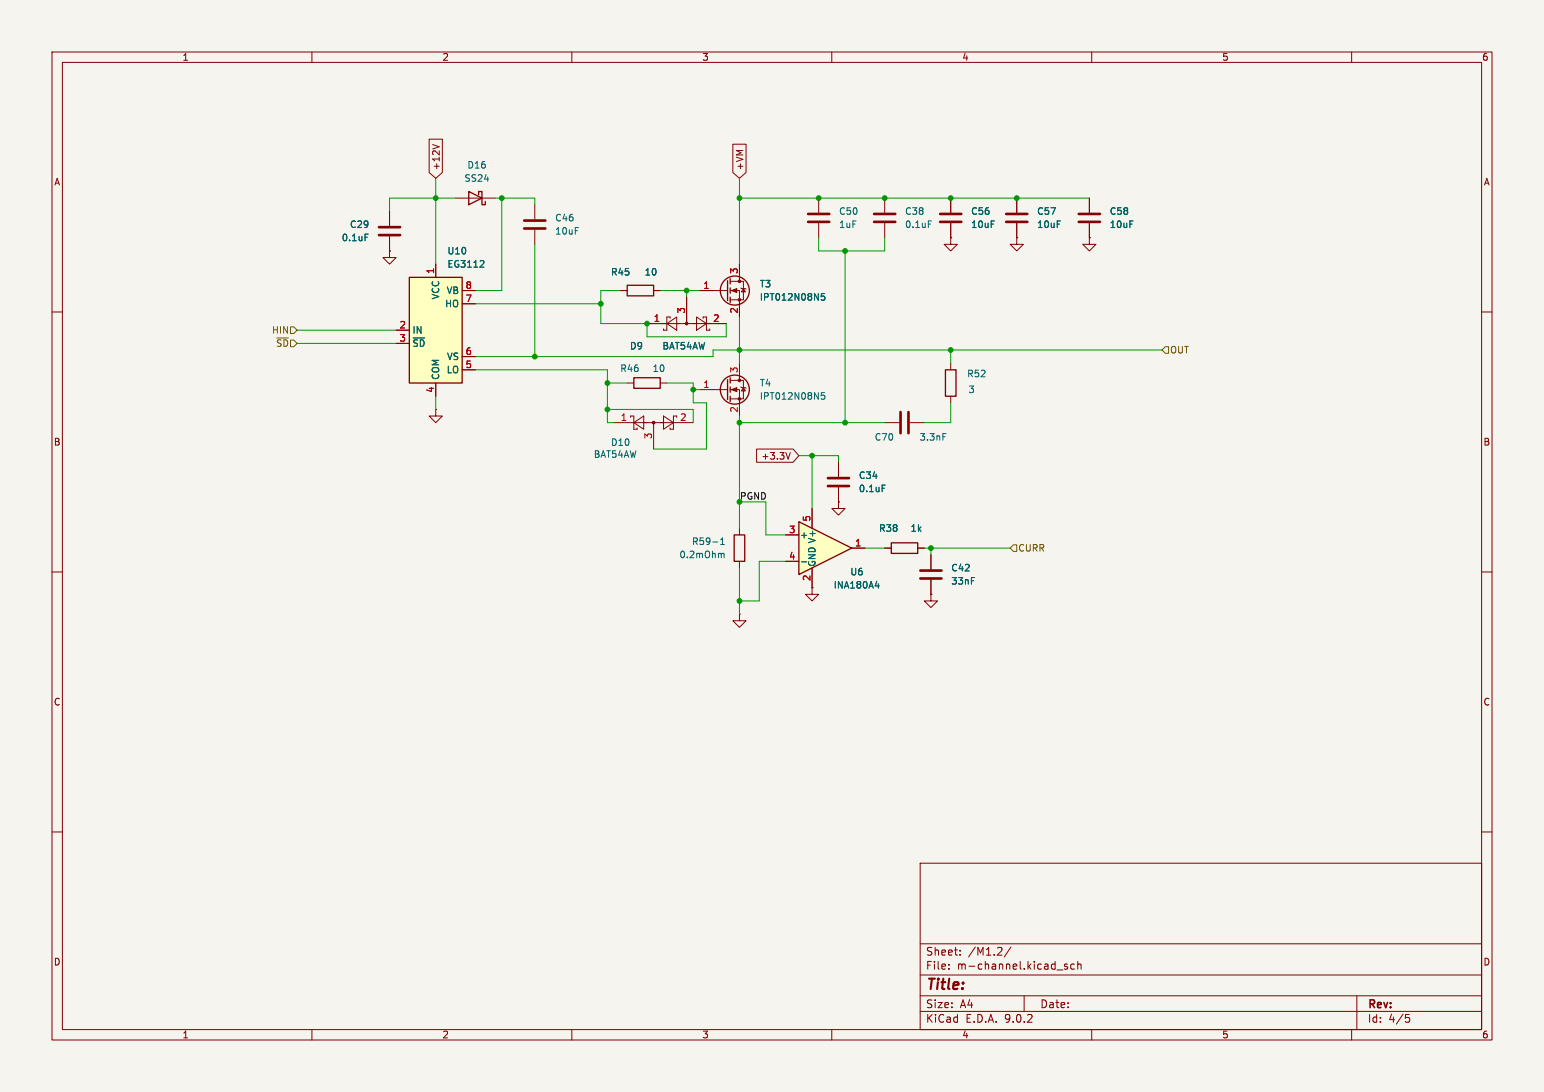
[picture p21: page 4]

Id: 4/5 Title: File: m-channel.kicad_sch Sheet: /M1.2/

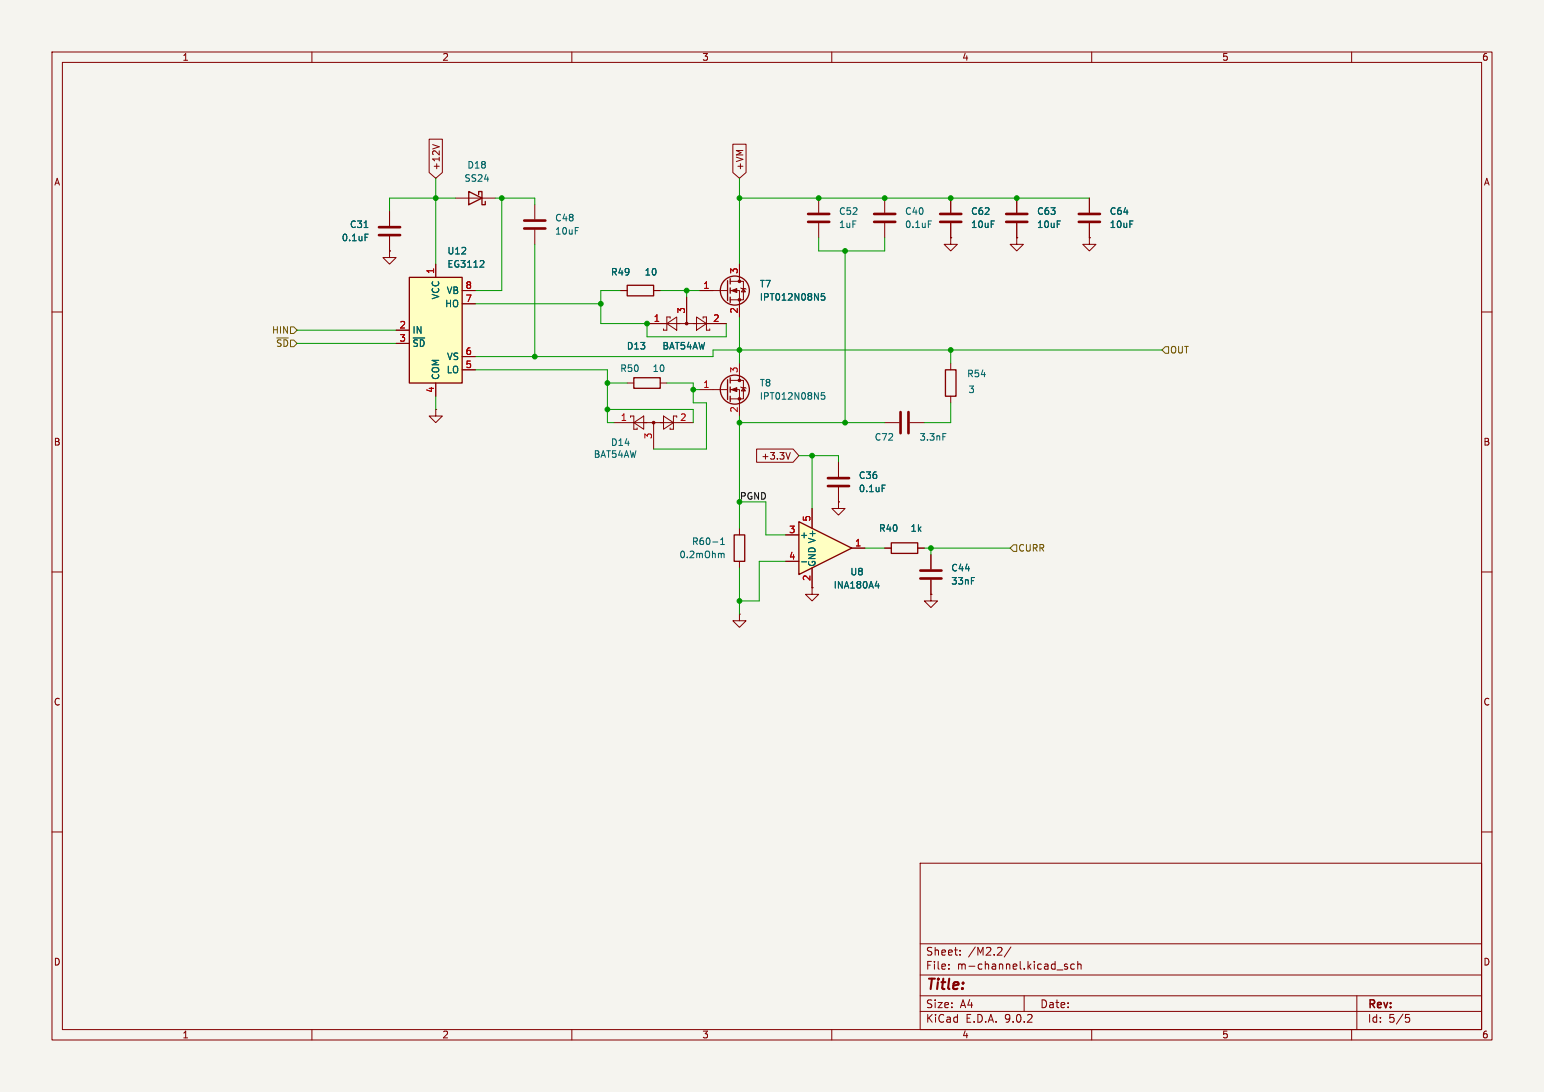
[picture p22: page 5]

Id: 5/5 Title: File: m-channel.kicad_sch Sheet: /M2.2/

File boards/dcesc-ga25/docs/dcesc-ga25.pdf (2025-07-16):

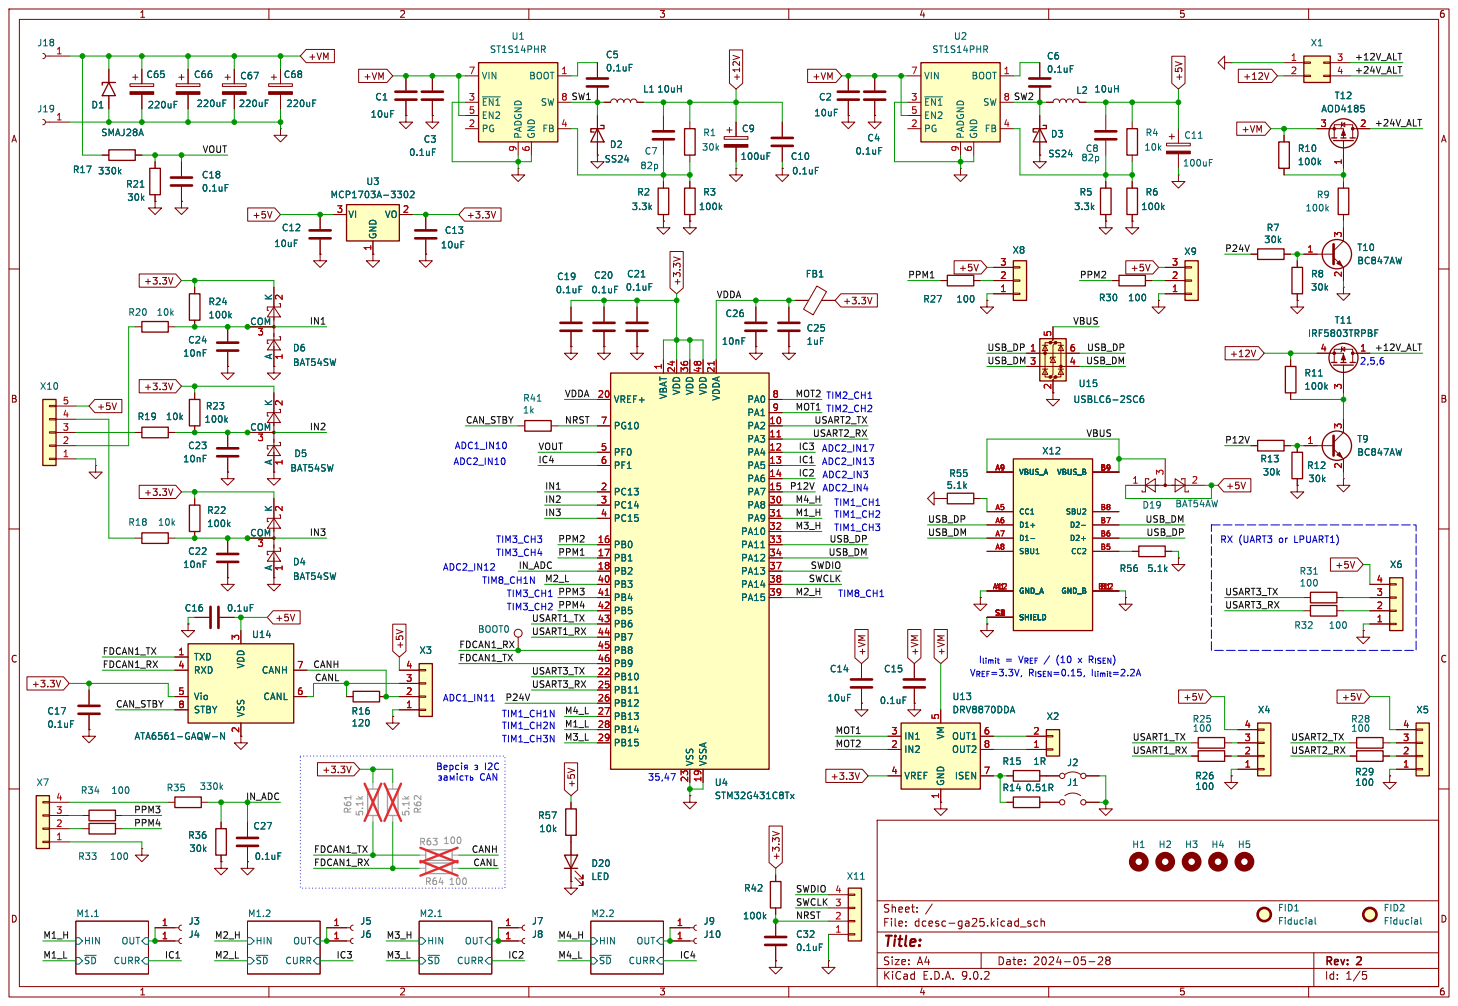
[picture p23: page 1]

1 VDD 24 VDD 36 VSS 23 VDD 48 VSSA 19 VDDA 21 PA0 8 PA1 9 PA2 10 PA3 11 PA4 12 PA5 13 PA6 14 PA7 15 PA8 30 PA9 31 PA10 32 PA11 33 PA12 34 PA13 37 PA14 38 PA15 39 U4STM32G431C8Tx R42
VOUTPPM3 PPM1

1 VDD 24 VDD 36 VSS 23 VDD 48 VSSA 19 VDDA 21 PA0 8 PA1 9 PA2 10 PA3 11 PA4 12 PA5 13 PA6 14 PA7 15 PA8 30 PA9 31 PA10 32 PA11 33 PA12 34 PA13 37 PA14 38 PA15 39 C14

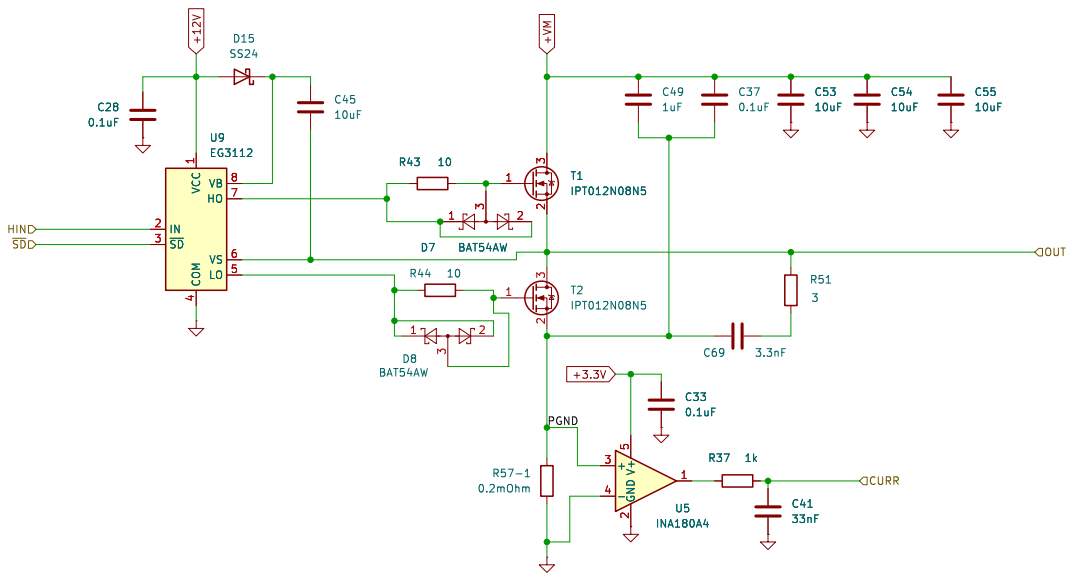
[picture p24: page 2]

Id: 2/5 Title: File: m-channel.kicad_sch Sheet: /M1.1/

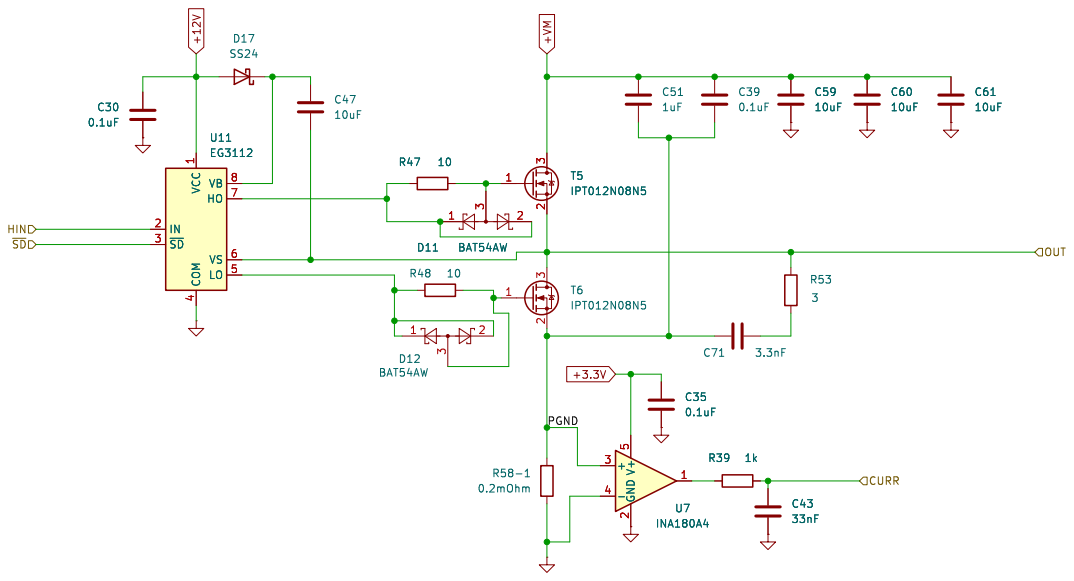
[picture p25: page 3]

Id: 3/5 Title: File: m-channel.kicad_sch Sheet: /M2.1/

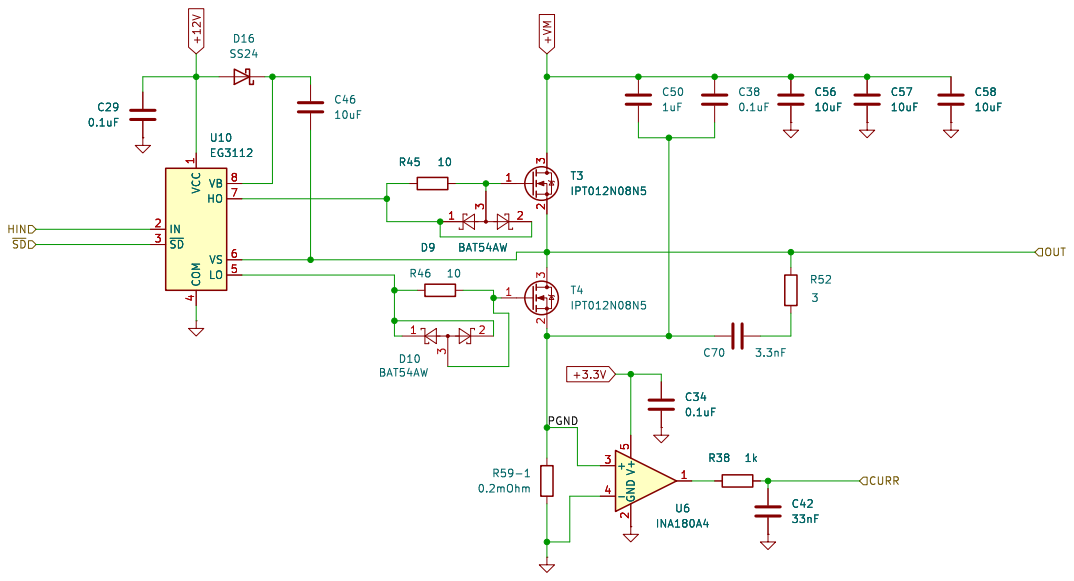
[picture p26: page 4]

Id: 4/5 Title: File: m-channel.kicad_sch Sheet: /M1.2/

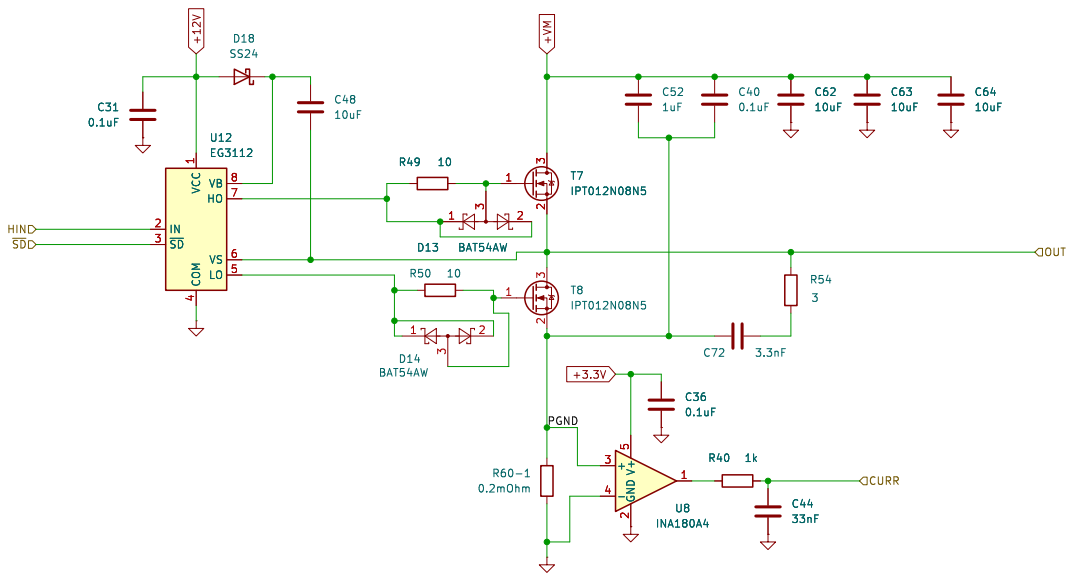
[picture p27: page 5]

Id: 5/5 Title: File: m-channel.kicad_sch Sheet: /M2.2/

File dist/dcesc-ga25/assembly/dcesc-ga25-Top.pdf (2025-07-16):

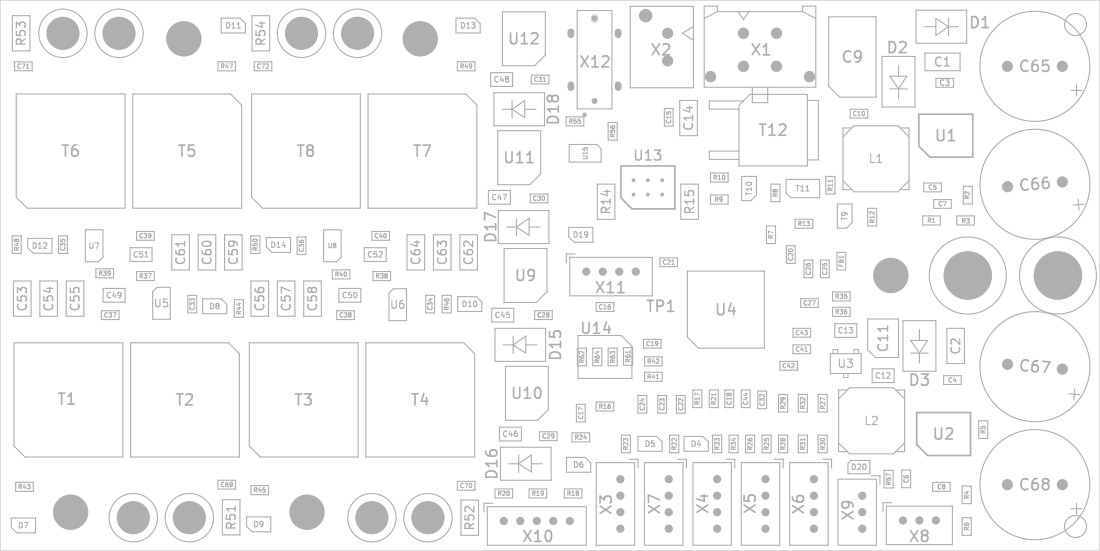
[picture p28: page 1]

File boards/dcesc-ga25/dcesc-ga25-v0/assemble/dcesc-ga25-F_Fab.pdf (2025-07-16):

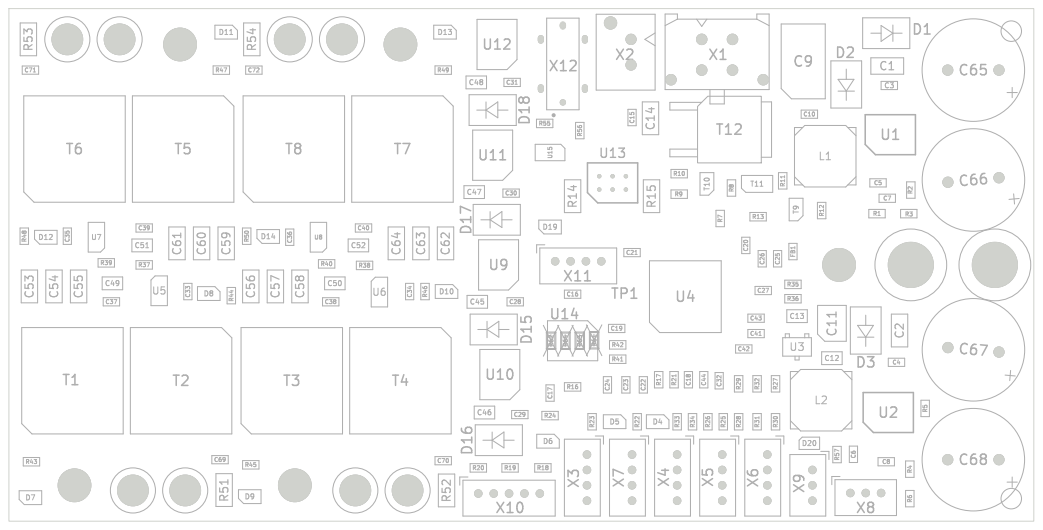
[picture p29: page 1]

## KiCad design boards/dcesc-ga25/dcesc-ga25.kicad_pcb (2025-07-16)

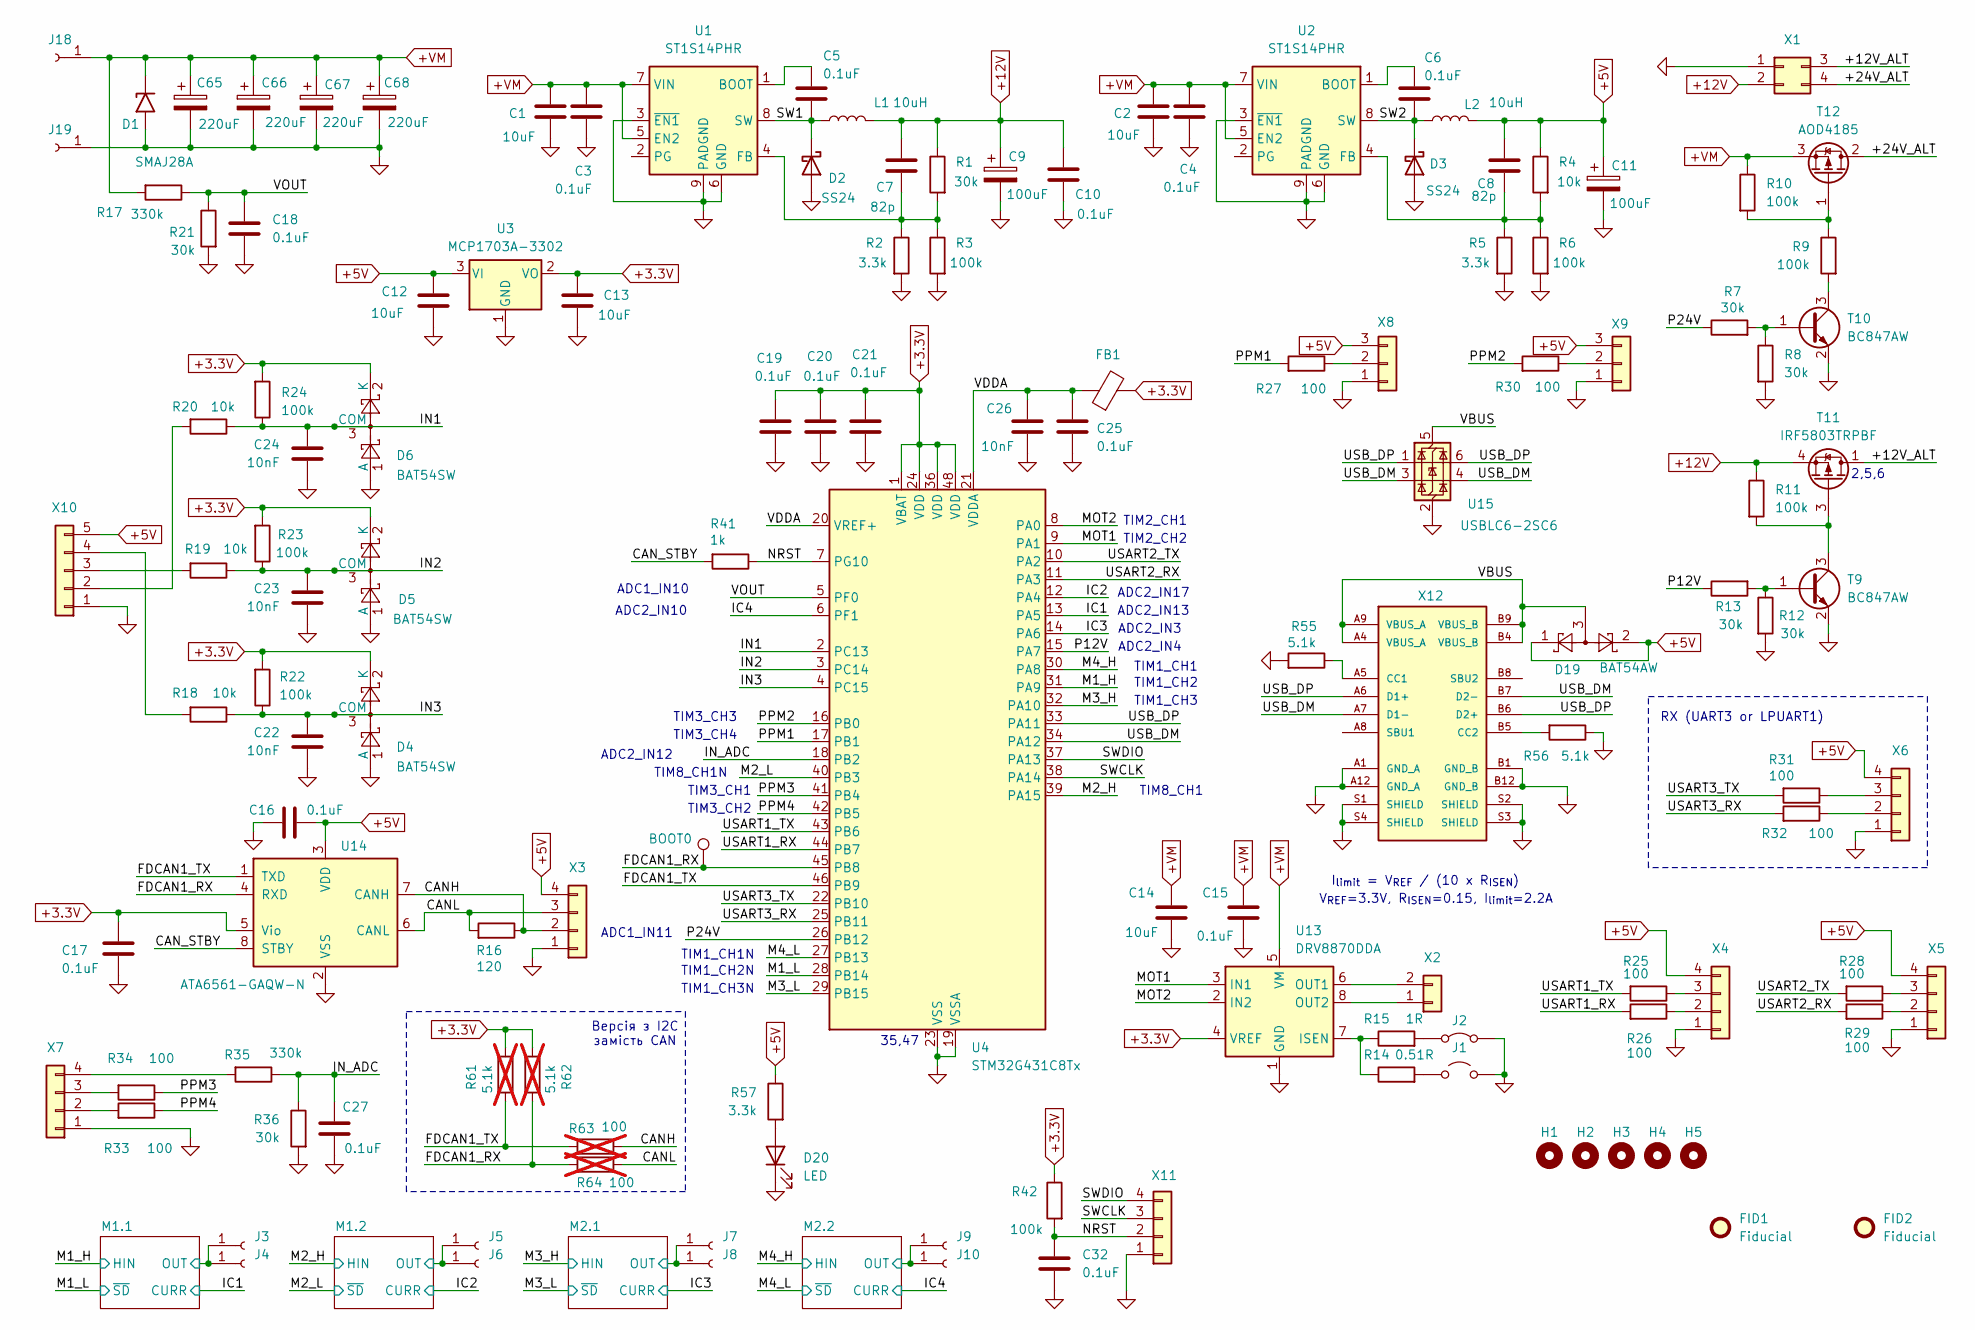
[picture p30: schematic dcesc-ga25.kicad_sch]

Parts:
C1, C2, C14: 10uF; C_1206_3216Metric
C3, C4, C5, C6, C10, C15, C16, C17, C18, C19, C20, C21, C25, C27, C32: 0.1uF; C_0603_1608Metric
C7, C8: 82p; C_0603_1608Metric
C9: 100uF; CP_EIA-7343-15_Kemet-W
C11: 100uF; CP_EIA-3528-12_Kemet-T
C12, C13: 10uF; C_0805_2012Metric
C22, C23, C24, C26: 10nF; C_0603_1608Metric
C65, C66, C67, C68: 220uF; CP_Radial_D10.0mm_P5.00mm
D1: SMAJ28A; D_SMA
D2, D3: SS24; D_SMA
D4, D5, D6: BAT54SW; SOT-323_SC-70
D19: BAT54AW; SOT-323_SC-70
D20: LED; LED_0805_2012Metric
FB1: FerriteBead; L_0603_1608Metric
FID1, FID2: Fiducial; Fiducial_1mm_Mask2mm
H1, H2, H3, H4, H5: MountingHole; MountingHole_3.2mm_M3
J1: Jumper_2_Open; SolderJumper-2_P1.3mm_Open_RoundedPad1.0x1.5mm
J2: Jumper_2_Bridged; SolderJumper-2_P1.3mm_Bridged_RoundedPad1.0x1.5mm
J3, J4, J5, J6, J7, J8, J9, J10: Conn_01x01_Socket; SolderWire-2.5sqmm_1x01_D2.4mm_OD4.4mm
J18, J19: Conn_01x01_Socket; SolderWire-6sqmm_1x01_D3.5mm_OD7mm
L1, L2: 10uH; Inductor_NR6028T100M
R1, R7, R8, R12, R13, R21, R36: 30k; R_0603_1608Metric
R2, R5, R57: 3.3k; R_0603_1608Metric
R3, R6, R9, R10, R11, R22, R23, R24, R42: 100k; R_0603_1608Metric
R4, R18, R19, R20: 10k; R_0603_1608Metric
R14: 0.51R; R_1206_3216Metric
R15: 1R; R_1206_3216Metric
R16: 120; R_0603_1608Metric
R17, R35: 330k; R_0603_1608Metric
R25, R26, R27, R28, R29, R30, R31, R32, R33, R34: 100; R_0603_1608Metric
R41: 1k; R_0603_1608Metric
R55, R56: 5.1k; R_0603_1608Metric
R61, R62: 5.1k; R_0603_1608Metric; not fitted
R63, R64: 100; R_0603_1608Metric; not fitted
T9, T10: BC847AW; SOT-323_SC-70
T11: IRF5803TRPBF; TSOP-6_1.65x3.05mm_P0.95mm
T12: AOD4185; TO-252-2
TP1: BOOT0; TestPoint_Pad_1.0x1.0mm
U1, U2: ST1S14PHR; TI_SO-PowerPAD-8
U3: MCP1703A-3302; MCP1703; MPN MCP1703T-3302E/CB
U4: STM32G431C8Tx; LQFP-48_7x7mm_P0.5mm
U13: DRV8870DDA; Texas_HTSOP-8-1EP_3.9x4.9mm_P1.27mm_EP2.95x4.9mm_Mask2.4x3.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
U14: ATA6561-GAQW-N; SOIC-8_3.9x4.9mm_P1.27mm
U15: USBLC6-2SC6; SOT-23-6
X1: Conn_02x02_Top_Bottom; Molex_Micro-Fit_3.0_43045-0412_2x02_P3.00mm_Vertical
X2: Conn_01x03; JST_XH_B2B-XH-AM_1x02_P2.50mm_Vertical
X3, X4, X5, X6, X7, X11: Conn_01x03; JST_ZH_B4B-ZR_1x04_P1.50mm_Vertical
X8, X9: Conn_01x03; JST_ZH_B3B-ZR_1x03_P1.50mm_Vertical
X10: Conn_01x03; JST_ZH_B5B-ZR_1x05_P1.50mm_Vertical
X12: USB4120-03-C_REVA; GCT_USB4120-03-C_REVA; PARTREV A

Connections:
+3.3V: C13.1, C17.1, C19.1, C20.1, C21.1, D4.2 (K), D5.2 (K), D6.2 (K), FB1.2, R22.2, R23.2, R24.2, R42.1, R61.1, R62.1, U3.2 (VO), U4.1 (VBAT), U4.24 (VDD), U4.36 (VDD), U4.48 (VDD), U13.4 (VREF), U14.5 (Vio); also elsewhere on the board
+5V: C8.1, C11.1, C12.1, C16.1, D19.1, D19.2, L2.2, R4.1, R57.1, U3.3 (VI), U14.3 (VDD), X3.4, X4.4, X5.4, X6.4, X8.3, X9.3, X10.5
+12V: C7.1, C9.1, C10.1, L1.2, R1.1, R11.1, T11.4 (S), X1.2; also elsewhere on the board
+VM: C1.1, C2.1, C3.1, C4.1, C14.1, C15.1, C65.1, C66.1, C67.1, C68.1, D1.1 (A1), J18.1, R10.1, R17.2, T12.3 (S), U1.5 (EN2), U1.7 (VIN), U2.5 (EN2), U2.7 (VIN), U13.5 (VM); also elsewhere on the board
/+12V_ALT: T11.1 (D), T11.2 (D), T11.5 (D), T11.6 (D), X1.3
/+24V_ALT: T12.2 (D), X1.4
/CANH: R16.1, R63.2, U14.7 (CANH), X3.2
/CANL: R16.2, R64.1, U14.6 (CANL), X3.3
/CAN_STBY: R41.2, U14.8 (STBY)
/FDCAN1_RX: R62.2, R64.2, TP1.1, U4.45 (PB8), U14.4 (RXD)
/FDCAN1_TX: R61.2, R63.1, U4.46 (PB9), U14.1 (TXD)
/IC1: U4.13 (PA5); also elsewhere on the board
/IC2: U4.12 (PA4); also elsewhere on the board
/IC3: U4.14 (PA6); also elsewhere on the board
/IC4: U4.6 (PF1); also elsewhere on the board
/IN1: C24.1, D6.3 (COM), R20.1, R24.1, U4.2 (PC13)
/IN2: C23.1, D5.3 (COM), R19.1, R23.1, U4.3 (PC14)
/IN3: C22.1, D4.3 (COM), R18.1, R22.1, U4.4 (PC15)
/IN_ADC: C27.1, R35.1, R36.1, U4.18 (PB2)
/M1.1/OUT: J3.1, J4.1; also elsewhere on the board
/M1.2/OUT: J5.1, J6.1; also elsewhere on the board
/M1_H: U4.31 (PA9); also elsewhere on the board
/M1_L: U4.28 (PB14); also elsewhere on the board
/M2.1/OUT: J7.1, J8.1; also elsewhere on the board
/M2.2/OUT: J9.1, J10.1; also elsewhere on the board
/M2_H: U4.39 (PA15); also elsewhere on the board
/M2_L: U4.40 (PB3); also elsewhere on the board
/M3_H: U4.32 (PA10); also elsewhere on the board
/M3_L: U4.29 (PB15); also elsewhere on the board
/M4_H: U4.30 (PA8); also elsewhere on the board
/M4_L: U4.27 (PB13); also elsewhere on the board
/MOT1: U4.9 (PA1), U13.3 (IN1)
/MOT2: U4.8 (PA0), U13.2 (IN2)
/NRST: C32.1, R41.1, R42.2, U4.7 (PG10), X11.2
/P12V: R13.1, U4.15 (PA7)
/P24V: R7.1, U4.26 (PB12)
/PPM1: R27.2, U4.17 (PB1)
/PPM2: R30.2, U4.16 (PB0)
/PPM3: R34.1, U4.41 (PB4)
/PPM4: R33.1, U4.42 (PB5)
/SW1: C5.2, D2.1 (K), L1.1, U1.8 (SW)
/SW2: C6.2, D3.1 (K), L2.1, U2.8 (SW)
/SWCLK: U4.38 (PA14), X11.3
/SWDIO: U4.37 (PA13), X11.4
/USART1_RX: R26.2, U4.44 (PB7)
/USART1_TX: R25.2, U4.43 (PB6)
/USART2_RX: R29.2, U4.11 (PA3)
/USART2_TX: R28.2, U4.10 (PA2)
/USART3_RX: R32.2, U4.25 (PB11)
/USART3_TX: R31.2, U4.22 (PB10)
/USB_DM: U4.34 (PA12), U15.3 (I/O2), U15.4 (I/O2), X12.A7 (D1-), X12.B7 (D2-)
/USB_DP: U4.33 (PA11), U15.1 (I/O1), U15.6 (I/O1), X12.A6 (D1+), X12.B6 (D2+)
/VBUS: D19.3, U15.5 (VBUS), X12.A4 (VBUS_A), X12.A9 (VBUS_A), X12.B4 (VBUS_B), X12.B9 (VBUS_B)
/VDDA: C25.1, C26.1, FB1.1, U4.20 (VREF+), U4.21 (VDDA)
/VOUT: C18.1, R17.1, R21.1, U4.5 (PF0)
GND: C1.2, C2.2, C3.2, C4.2, C9.2, C10.2, C11.2, C12.2, C13.2, C14.2, C15.2, C16.2, C17.2, C18.2, C19.2, C20.2, C21.2, C22.2, C23.2, C24.2, C25.2, C26.2, C27.2, C32.2, C65.2, C66.2, C67.2, C68.2, D1.2 (A2), D2.2 (A), D3.2 (A), D4.1 (A), D5.1 (A), D6.1 (A), D20.1 (K), J1.2 (B), J2.2 (B), J19.1, R2.2, R3.2, R5.2, R6.2, R8.2, R12.2, R21.2, R36.2, R55.2, R56.1, T9.2 (E), T10.2 (E), U1.3 (~EN1), U1.6 (GND), U1.9 (PADGND), U2.3 (~EN1), U2.6 (GND), U2.9 (PADGND), U3.1 (GND), U4.19 (VSSA), U4.23 (VSS), U4.35 (VSS), U4.47 (VSS), U13.1 (GND), U13.9 (GND), U14.2 (VSS), U15.2 (GND), X1.1, X3.1, X4.1, X5.1, X6.1, X7.1, X8.1, X9.1, X10.1, X11.1, X12.A1 (GND_A), X12.A12 (GND_A), X12.B1 (GND_B), X12.B12 (GND_B), X12.S1 (SHIELD), X12.S2 (SHIELD), X12.S3 (SHIELD), X12.S4 (SHIELD); also elsewhere on the board
unnamed: D20.2 (A), R57.2
unnamed: J1.1 (A), R14.2
unnamed: J2.1 (A), R15.2
unnamed: R12.1, R13.2, T9.1 (B)
unnamed: R7.2, R8.1, T10.1 (B)
unnamed: R9.2, T10.3 (C)
unnamed: R11.2, T9.3 (C), T11.3 (G)
unnamed: R9.1, R10.2, T12.1 (G)
unnamed: C5.1, U1.1 (BOOT)
unnamed: C7.2, R1.2, R2.1, R3.1, U1.4 (FB)
unnamed: C6.1, U2.1 (BOOT)
unnamed: C8.2, R4.2, R5.1, R6.1, U2.4 (FB)
unnamed: R14.1, R15.1, U13.7 (ISEN)
unnamed: U13.6 (OUT1), X2.2
unnamed: U13.8 (OUT2), X2.1
unnamed: R26.1, X4.2
unnamed: R25.1, X4.3
unnamed: R29.1, X5.2
unnamed: R28.1, X5.3
unnamed: R32.1, X6.2
unnamed: R31.1, X6.3
unnamed: R33.2, X7.2
unnamed: R34.2, X7.3
unnamed: R35.2, X7.4
unnamed: R27.1, X8.2
unnamed: R30.1, X9.2
unnamed: R20.2, X10.2
unnamed: R19.2, X10.3
unnamed: R18.2, X10.4
unnamed: R55.1, X12.A5 (CC1)
unnamed: R56.2, X12.B5 (CC2)

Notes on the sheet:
TIM1_CH2N
TIM1_CH2
TIM3_CH1
ADC2_IN13
Версія з I2C замість CAN
TIM1_CH1
2,5,6
ADC1_IN10
TIM8_CH1
TIM1_CH1N
TIM3_CH4
ADC2_IN12
TIM3_CH3
RX (UART3 or LPUART1)
ADC1_IN11
I_{limit} = V_{REF} / (10 x R_{ISEN})
TIM1_CH3
TIM1_CH3N
V_{REF}=3.3V, R_{ISEN}=0.15, I_{limit}=2.2A
ADC2_IN17
TIM8_CH1N
TIM3_CH2
ADC2_IN4
ADC2_IN3
TIM2_CH2
ADC2_IN10
35,47
TIM2_CH1

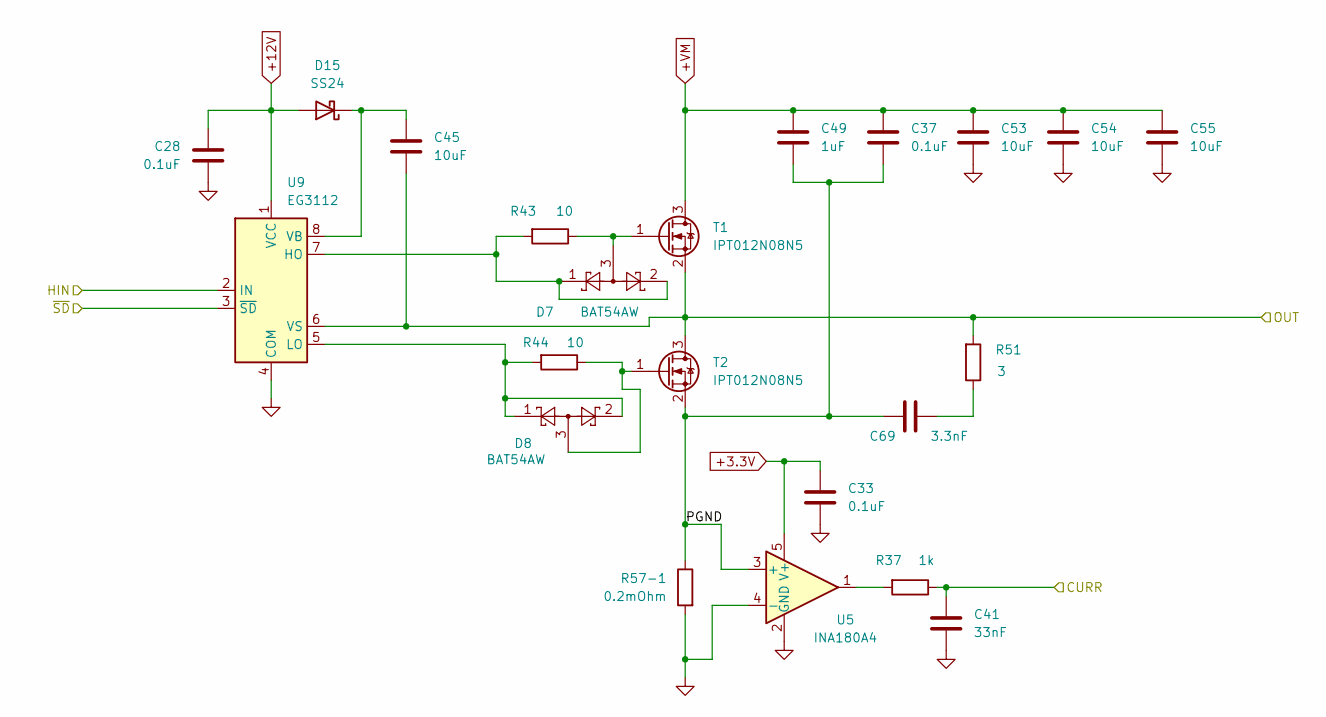
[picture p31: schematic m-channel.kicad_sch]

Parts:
C28, C33, C37: 0.1uF; C_0603_1608Metric
C41: 33nF; C_0603_1608Metric
C45: 10uF; C_0805_2012Metric
C49: 1uF; C_0805_2012Metric
C53, C54, C55: 10uF; C_1206_3216Metric
C69: 3.3nF; C_0603_1608Metric
D7, D8: BAT54AW; SOT-323_SC-70
D15: SS24; D_SMA
R37: 1k; R_0603_1608Metric
R43, R44: 10; R_0603_1608Metric
R51: 3; R_1206_3216Metric
R57-1: 0.2mOhm; R_SHUNT
T1, T2: IPT012N08N5; Infineon_PG-HSOF-8-1
U5: INA180A4; SOT-23-5
U9: EG3112; SOP-8_3.9x4.9mm_P1.27mm

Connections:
+3.3V: C33.1, U5.5 (V+); also elsewhere on the board
+12V: C28.1, D15.2 (A), U9.1 (VCC); also elsewhere on the board
+VM: C37.1, C49.1, C53.1, C54.1, C55.1, T1.3 (D); also elsewhere on the board
/IC1: C41.1, R37.1; also elsewhere on the board
/M1.1/OUT: C45.2, R51.2, T1.2 (S), T2.3 (D), U9.6 (VS); also elsewhere on the board
/M1.1/PGND: C37.2, C49.2, C69.2, R57-1.1, T2.2 (S), U5.3 (+)
/M1_H: U9.2 (IN); also elsewhere on the board
/M1_L: U9.3 (~SD); also elsewhere on the board
GND: C28.2, C33.2, C41.2, C53.2, C54.2, C55.2, R57-1.2, U5.2 (GND), U5.4 (-), U9.4 (COM); also elsewhere on the board
unnamed: C69.1, R51.1
unnamed: C45.1, D15.1 (K), U9.8 (VB)
unnamed: R37.2, U5.1
unnamed: D7.3, R43.1, T1.1 (G)
unnamed: D8.3, R44.1, T2.1 (G)
unnamed: D7.1, D7.2, R43.2, U9.7 (HO)
unnamed: D8.1, D8.2, R44.2, U9.5 (LO)

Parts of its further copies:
C29, C30, C31, C34, C35, C36, C38, C39, C40: 0.1uF; C_0603_1608Metric
C42, C43, C44: 33nF; C_0603_1608Metric
C46, C47, C48: 10uF; C_0805_2012Metric
C50, C51, C52: 1uF; C_0805_2012Metric
C56, C57, C58, C59, C60, C61, C62, C63, C64: 10uF; C_1206_3216Metric
C70, C71, C72: 3.3nF; C_0603_1608Metric
D9, D10, D11, D12, D13, D14: BAT54AW; SOT-323_SC-70
D16, D17, D18: SS24; D_SMA
R38, R39, R40: 1k; R_0603_1608Metric
R45, R46, R47, R48, R49, R50: 10; R_0603_1608Metric
R52, R53, R54: 3; R_1206_3216Metric
R58-1, R59-1, R60-1: 0.2mOhm; R_SHUNT
T3, T4, T5, T6, T7, T8: IPT012N08N5; Infineon_PG-HSOF-8-1
U6, U7, U8: INA180A4; SOT-23-5
U10, U11, U12: EG3112; SOP-8_3.9x4.9mm_P1.27mm

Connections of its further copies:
+3.3V: C34.1, C35.1, C36.1, U6.5 (V+), U7.5 (V+), U8.5 (V+); also elsewhere on the board
+12V: C29.1, C30.1, C31.1, D16.2 (A), D17.2 (A), D18.2 (A), U10.1 (VCC), U11.1 (VCC), U12.1 (VCC); also elsewhere on the board
+VM: C38.1, C39.1, C40.1, C50.1, C51.1, C52.1, C56.1, C57.1, C58.1, C59.1, C60.1, C61.1, C62.1, C63.1, C64.1, T3.3 (D), T5.3 (D), T7.3 (D); also elsewhere on the board
/IC2: C42.1, R38.1; also elsewhere on the board
/IC3: C43.1, R39.1; also elsewhere on the board
/IC4: C44.1, R40.1; also elsewhere on the board
/M1.2/OUT: C46.2, R52.2, T3.2 (S), T4.3 (D), U10.6 (VS); also elsewhere on the board
/M1.2/PGND: C38.2, C50.2, C70.2, R59-1.1, T4.2 (S), U6.3 (+)
/M2.1/OUT: C47.2, R53.2, T5.2 (S), T6.3 (D), U11.6 (VS); also elsewhere on the board
/M2.1/PGND: C39.2, C51.2, C71.2, R58-1.1, T6.2 (S), U7.3 (+)
/M2.2/OUT: C48.2, R54.2, T7.2 (S), T8.3 (D), U12.6 (VS); also elsewhere on the board
/M2.2/PGND: C40.2, C52.2, C72.2, R60-1.1, T8.2 (S), U8.3 (+)
/M2_H: U10.2 (IN); also elsewhere on the board
/M2_L: U10.3 (~SD); also elsewhere on the board
/M3_H: U11.2 (IN); also elsewhere on the board
/M3_L: U11.3 (~SD); also elsewhere on the board
/M4_H: U12.2 (IN); also elsewhere on the board
/M4_L: U12.3 (~SD); also elsewhere on the board
GND: C29.2, C30.2, C31.2, C34.2, C35.2, C36.2, C42.2, C43.2, C44.2, C56.2, C57.2, C58.2, C59.2, C60.2, C61.2, C62.2, C63.2, C64.2, R58-1.2, R59-1.2, R60-1.2, U6.2 (GND), U6.4 (-), U7.2 (GND), U7.4 (-), U8.2 (GND), U8.4 (-), U10.4 (COM), U11.4 (COM), U12.4 (COM); also elsewhere on the board
unnamed: C70.1, R52.1
unnamed: C71.1, R53.1
unnamed: C72.1, R54.1
unnamed: C46.1, D16.1 (K), U10.8 (VB)
unnamed: C47.1, D17.1 (K), U11.8 (VB)
unnamed: C48.1, D18.1 (K), U12.8 (VB)
unnamed: R38.2, U6.1
unnamed: R39.2, U7.1
unnamed: R40.2, U8.1
unnamed: D9.3, R45.1, T3.1 (G)
unnamed: D10.3, R46.1, T4.1 (G)
unnamed: D11.3, R47.1, T5.1 (G)
unnamed: D12.3, R48.1, T6.1 (G)
unnamed: D13.3, R49.1, T7.1 (G)
unnamed: D14.3, R50.1, T8.1 (G)
unnamed: D9.1, D9.2, R45.2, U10.7 (HO)
unnamed: D10.1, D10.2, R46.2, U10.5 (LO)
unnamed: D11.1, D11.2, R47.2, U11.7 (HO)
unnamed: D12.1, D12.2, R48.2, U11.5 (LO)
unnamed: D13.1, D13.2, R49.2, U12.7 (HO)
unnamed: D14.1, D14.2, R50.2, U12.5 (LO)

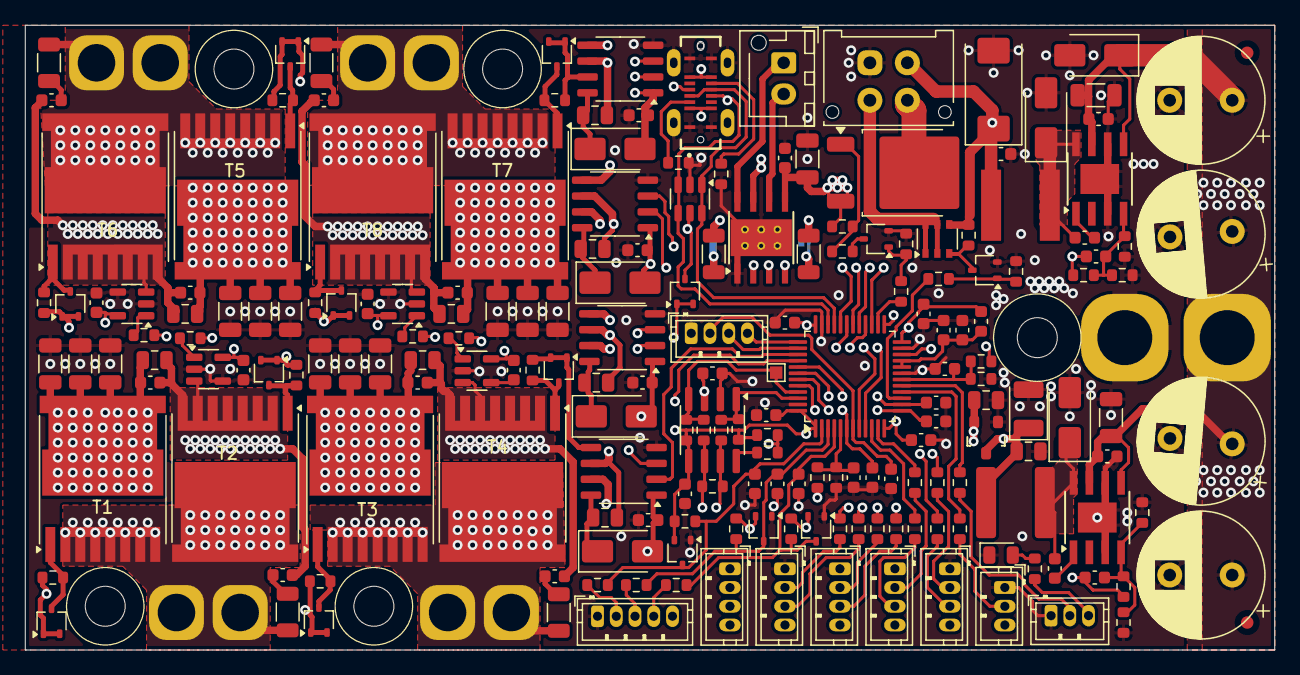
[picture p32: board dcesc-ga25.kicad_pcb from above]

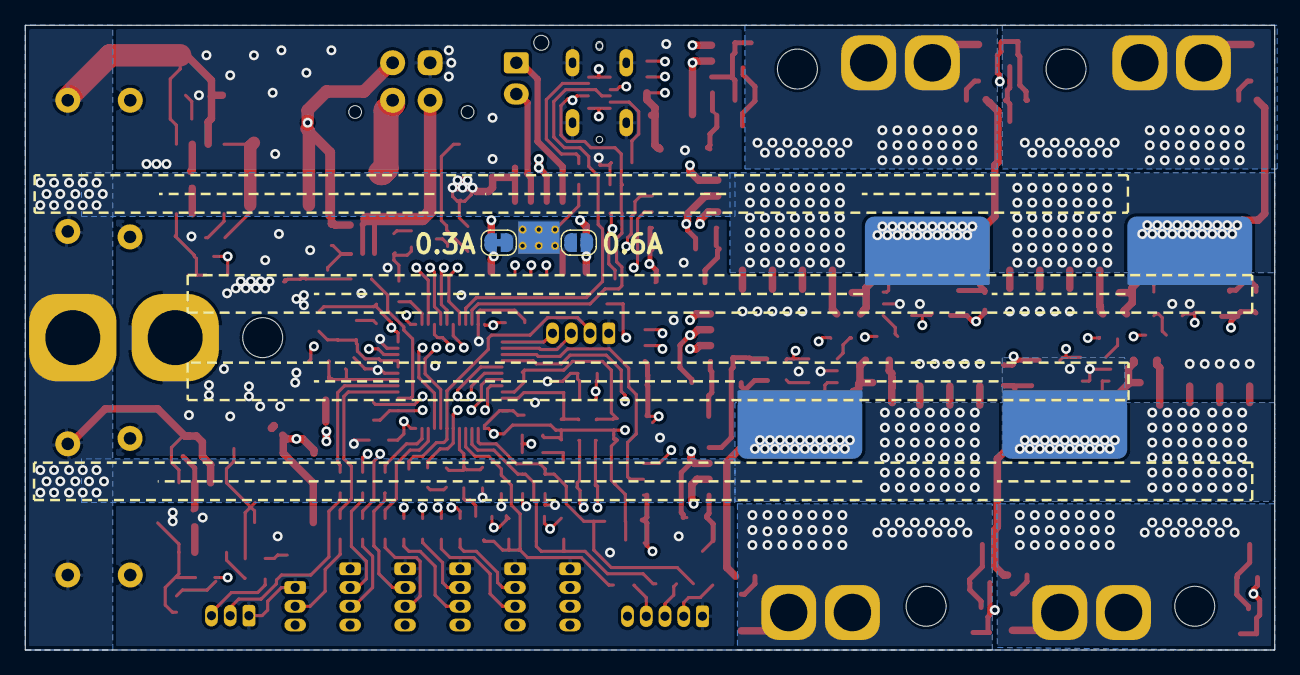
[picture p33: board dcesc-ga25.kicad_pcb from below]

Board: 4 copper layers, 100.0 x 50.0 mm, 219 parts (6 on the bottom side), 119 nets.

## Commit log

2025-07-16 Розведено.
    [43025-0400--3DModel-STEP-390490.STEP, 430450427--3DModel-STEP-56544.STEP, B2B-XH-A-LF--SN---3DModel-STEP-269445.STEP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]
2025-07-16 Плати замовлено.
    [dcesc-ga25-B_Cu.gbl, dcesc-ga25-B_Mask.gbs, dcesc-ga25-B_Silkscreen.gbo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]
